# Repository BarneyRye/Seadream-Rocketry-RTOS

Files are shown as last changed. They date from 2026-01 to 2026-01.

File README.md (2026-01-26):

# Seadream Rocketry PCB and Code
 Kicad files include schematic, pcb, extra symbols, footprints 3d files and also the production files for JLCPCB </br>
 Included code written in Platform.io on VSCode, uses prebuilt libaries and freeRTOS, one task for sensor reading and audio, other task for writing to SD

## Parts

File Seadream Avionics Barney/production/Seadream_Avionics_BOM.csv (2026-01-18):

Reference | Qty | Value | DNP | Exclude from BOM | Exclude from Board | Footprint | Datasheet | Description | Part NO.
C1,C3,C4,C5,C6,C7,C12,C13,C14 | 9 | 100nF |  |  |  | Capacitor_SMD:C_0402_1005Metric | https://jlcpcb.com/api/file/downloadByFileSystemAccessId/8579707269996871680 | CL05B104KO5NNNC | C1525
C2,C8,C9,C10 | 4 | 10uF |  |  |  | Capacitor_SMD:C_0603_1608Metric | https://jlcpcb.com/api/file/downloadByFileSystemAccessId/8579707107920437248 | CL10A106KP8NNNC | C19702
C11 | 1 | 22uF |  |  |  | Capacitor_SMD:C_0805_2012Metric | https://jlcpcb.com/api/file/downloadByFileSystemAccessId/8579706866429190144 | CL21A226MAQNNNE | C45783
C15 | 1 | 1uF |  |  |  | Capacitor_SMD:C_0402_1005Metric | https://jlcpcb.com/api/file/downloadByFileSystemAccessId/8579707174974914560 | CL05A105KA5NQNC | C52923
D1,D2,D3 | 3 | LED |  |  |  | LED_SMD:LED_0805_2012Metric | https://jlcpcb.com/api/file/downloadByFileSystemAccessId/8550724080677908480 | NCD0805R1 | C84256
J1,J3 | 2 | B2B-PH-K-S(LF)(SN) |  |  |  | Connector_JST:JST_PH_B2B-PH-K_1x02_P2.00mm_Vertical | https://jlcpcb.com/api/file/downloadByFileSystemAccessId/8588889744620572672 | B2B-PH-K-S(LF)(SN) | C131337
J2 | 1 | TYPE-C16PIN |  |  |  | 2FOOTPRINTS:SHOUHAN_TYPE-C_16PIN_2MD__073_ | https://jlcpcb.com/api/file/downloadByFileSystemAccessId/8588893971980423168 | TYPE-C16PIN | C393939
MICRO_SD1 | 1 | TF-01A |  |  |  | 2FOOTPRINTS:TF-01A | https://jlcpcb.com/api/file/downloadByFileSystemAccessId/8588894212661764096 | TF-01A | C91145
R1,R2,R11 | 3 | 10k |  |  |  | Resistor_SMD:R_0402_1005Metric | https://jlcpcb.com/api/file/downloadByFileSystemAccessId/8588881989415931904 | 0402WGJ0103TCE | C25531
R3,R4 | 2 | 4k7 |  |  |  | Resistor_SMD:R_0402_1005Metric | https://jlcpcb.com/api/file/downloadByFileSystemAccessId/8579705941367193600 | 0402WGF4701TCE | C25900
R5 | 1 | 330 |  |  |  | Resistor_SMD:R_0603_1608Metric | https://jlcpcb.com/api/file/downloadByFileSystemAccessId/8579706223213461504 | 0603WAF3300T5E | C23138
R7,R10 | 2 | 5k1 |  |  |  | Resistor_SMD:R_0402_1005Metric | https://jlcpcb.com/api/file/downloadByFileSystemAccessId/8579706036003409920 | 0402WGF5101TCE | C25905
R8,R9 | 2 | 220 |  |  |  | Resistor_SMD:R_0603_1608Metric | https://jlcpcb.com/api/file/downloadByFileSystemAccessId/8579706178210742272 | 0603WAF2200T5E | C22962
S1 | 1 | KMR221GLFS |  |  |  | 2FOOTPRINTS:SW_KMR221GLFS | https://jlcpcb.com/api/file/downloadByFileSystemAccessId/8588916370310369280 | KMR221GLFS | C72443
SW1 | 1 | SSSS810701 |  |  |  | 2FOOTPRINTS:SW-SMD_SSSS810701 | https://jlcpcb.com/api/file/downloadByFileSystemAccessId/8588917637593751552 | SSSS810701 | C97433
U1 | 1 | BMP280 |  |  |  | 2FOOTPRINTS:XDCR_BMP280 | https://jlcpcb.com/api/file/downloadByFileSystemAccessId/8588881905890156544 | BMP280 | C83291
U2 | 1 | ESP32-S3-MINI-1U-N8 |  |  |  | RF_Module:ESP32-S2-MINI-1U | https://documentation.espressif.com/esp32-s3-mini-1_mini-1u_datasheet_en.pdf | ESP32-S3-MINI-1U-N8 | C2980299
U3 | 1 | LSM6DSO32TR |  |  |  | 2FOOTPRINTS:XDCR_LSM6DSO32TR | https://jlcpcb.com/api/file/downloadByFileSystemAccessId/8588926227138138112 | LSM6DSO32TR | C1864162
U4 | 1 | LD1117S33TR |  |  |  | 2FOOTPRINTS:SOT230P700X180-4N | https://jlcpcb.com/api/file/downloadByFileSystemAccessId/8586198736901459968 | LD1117S33TR | C86781
U5 | 1 | SHT40-AD1B-R3 |  |  |  | 2FOOTPRINTS:SHT4X | https://jlcpcb.com/api/file/downloadByFileSystemAccessId/8588907595537399808 | SHT40-AD1B-R3 | C2848306
U6 | 1 | LD39200PU33R |  |  |  | 2FOOTPRINTS:SON95P300X300X100-7N | https://jlcpcb.com/api/file/downloadByFileSystemAccessId/8588886586771845120 | LD39200PU33R | C222192
U7 | 1 | MAX98357AETE_T |  |  |  | 2FOOTPRINTS:QFN50P300X300X80-17N | https://jlcpcb.com/api/file/downloadByFileSystemAccessId/8588886693302161408 | MAX98357AETE_T | C910544

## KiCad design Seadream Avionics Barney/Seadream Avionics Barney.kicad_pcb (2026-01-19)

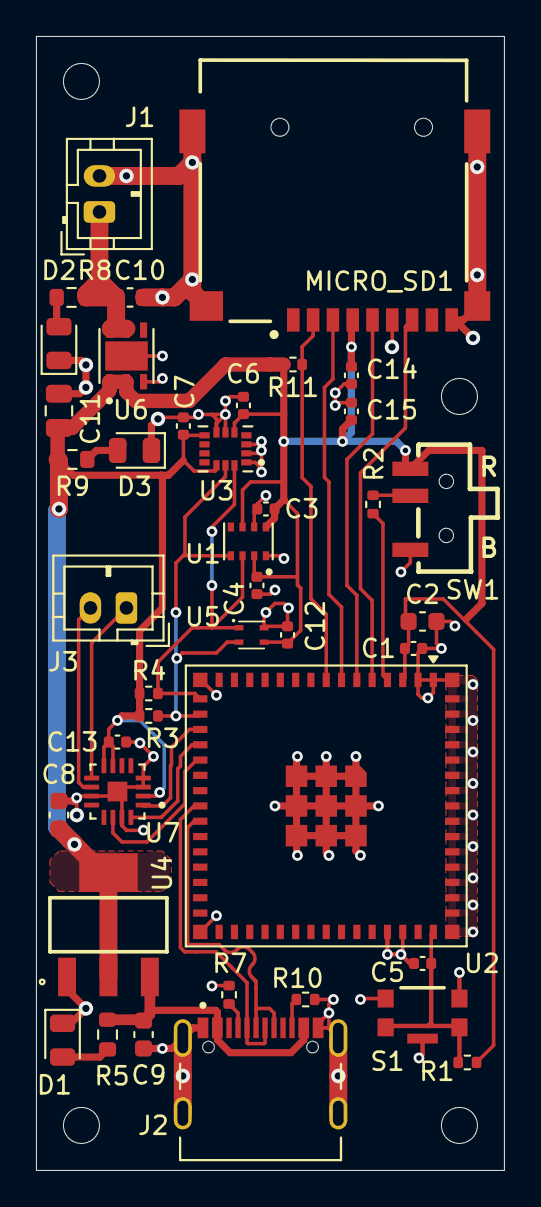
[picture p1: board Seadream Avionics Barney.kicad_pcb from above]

Board: 2 copper layers, 26.0 x 63.0 mm, 41 parts (0 on the bottom side), 25 nets.

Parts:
C1, C3, C4, C5, C6, C7, C12, C13, C14: 100nF; C_0402_1005Metric
C2, C8, C9, C10: 10uF; C_0603_1608Metric
C11: 22uF; C_0805_2012Metric
C15: 1uF; C_0402_1005Metric
D1, D2, D3: LED; LED_0805_2012Metric
J1, J3: B2B-PH-K-S(LF)(SN); JST_PH_B2B-PH-K_1x02_P2.00mm_Vertical
J2: C393939; SHOUHAN_TYPE-C_16PIN_2MD__073_
MICRO_SD1: C91145; TF-01A
R1, R2, R11: 10k; R_0402_1005Metric
R3, R4: 4k7; R_0402_1005Metric
R5: 330; R_0603_1608Metric
R7, R10: 5k1; R_0402_1005Metric
R8, R9: 220; R_0603_1608Metric
S1: KMR221GLFS; SW_KMR221GLFS
SW1: SSSS810701; SW-SMD_SSSS810701
U1: BMP280; XDCR_BMP280
U2: ESP32-S3-MINI-1U-N8; ESP32-S2-MINI-1U
U3: LSM6DSO32TR; XDCR_LSM6DSO32TR
U4: LD1117S33TR; SOT230P700X180-4N
U5: SHT40-AD1B-R3; SHT4X
U6: LD39200PU33R; SON95P300X300X100-7N
U7: MAX98357AETE_T; QFN50P300X300X80-17N

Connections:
+3.3V: C1.2, C2.2, C3.1, C4.1, C6.1, C7.1, C8.1, C11.2, C12.1, C13.1, C14.2, C15.2, MICRO_SD1.4 (VDD), R1.2, R3.1, R4.1, R9.1, R11.1, SW1.3 (C), U1.2 (CSB), U1.6 (VDDIO), U1.8 (VDD), U2.3 (3V3), U3.5 (VDDIO), U3.8 (VDD), U3.12 (CS), U4.2 (OUT), U4.4 (OUT), U5.3 (VDD), U6.1 (OUT), U6.2 (SENSE), U7.2 (GAIN_SLOT), U7.7 (VDD), U7.8 (VDD)
/BOOT: R2.2, U2.4 (IO0)
/CD: MICRO_SD1.2 (CD/DAT3), R11.2, U2.8 (IO4)
/D+: J2.A6 (DP1), J2.B6 (DP2), U2.24 (IO20)
/D-: J2.A7 (DN1), J2.B7 (DN2), U2.23 (IO19)
/EN: C5.2, R1.1, S1.1, S1.4, U2.45 (EN)
/IO12: R4.2, U1.3 (SDI), U2.16 (IO12), U3.14 (SDA), U5.1 (SDA)
/IO13: R3.2, U1.4 (SCK), U2.17 (IO13), U3.13 (SCL), U5.2 (SCL)
/IO14: U2.18 (IO14), U7.1 (DIN)
/IO15: U2.19 (IO15), U7.16 (BCLK)
/IO16: U2.20 (IO16), U7.14 (LRCLK)
/MISO: MICRO_SD1.7 (DAT0), U2.5 (IO1)
/MOSI: MICRO_SD1.3 (CMD), U2.7 (IO3)
/OUT+: J3.1, U7.9 (OUTP)
/OUT-: J3.2, U7.10 (OUTN)
/SCK: MICRO_SD1.5 (CLK), U2.6 (IO2)
/USB 5V: C9.1, J2.A4_B9 (VBUS_A), J2.B4_A9 (VBUS_B), R5.1, U4.3 (IN)
GND: C1.1, C2.1, C3.2, C4.2, C5.1, C6.2, C7.2, C8.2, C9.2, C10.1, C11.1, C12.2, C13.2, C14.1, C15.1, D1.1 (K), D2.1 (K), D3.1 (K), J1.2, J2.A1_B12 (GND_A), J2.B1_A12 (GND_B), J2.SH1 (SHIELD), J2.SH2 (SHIELD), J2.SH3 (SHIELD), J2.SH4 (SHIELD), MICRO_SD1.6 (VSS), MICRO_SD1.CD1 (CD), MICRO_SD1.MP1 (SHIELD), MICRO_SD1.MP2 (SHIELD), MICRO_SD1.MP3 (SHIELD), MICRO_SD1.MP4 (SHIELD), R7.1, R10.2, S1.2, S1.3, S1.5, SW1.1 (A), U1.1 (GND), U1.7 (GND), U2.1 (GND1), U2.2 (GND1), U2.42 (GND1), U2.43 (GND1), U2.46 (GND1), U2.47 (GND1), U2.48 (GND1), U2.49 (GND1), U2.50 (GND1), U2.51 (GND1), U2.52 (GND1), U2.53 (GND1), U2.54 (GND2), U2.55 (GND2), U2.56 (GND2), U2.57 (GND2), U2.58 (GND2), U2.59 (GND2), U2.60 (GND3), U2.61, U2.62 (GND2), U2.63 (GND2), U2.64 (GND2), U2.65 (GND2), U3.1 (SDO/SA0), U3.2 (SDX), U3.3 (SCX), U3.6 (GND), U3.7 (GND), U4.1 (GND), U5.4 (VSS), U6.3 (GND), U6.7 (EXP), U7.3 (GND), U7.4 (SD_MODE), U7.11 (GND), U7.15 (GND), U7.17 (EP)
unnamed: D1.2 (A), R5.2
unnamed: D2.2 (A), R8.2
unnamed: D3.2 (A), R9.2
unnamed: C10.2, J1.1, R8.1, U6.5 (EN), U6.6 (IN)
unnamed: J2.A5 (CC1), R7.2
unnamed: J2.B5 (CC2), R10.1
unnamed: R2.1, SW1.2 (B)

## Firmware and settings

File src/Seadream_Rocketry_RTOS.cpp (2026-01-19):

//If working in arduino IDE, to allow use of esp32 boards
//https://espressif.github.io/arduino-esp32/package_esp32_index.json
//File->Preferences->Additional Board Manager URLs
//Boards Manager -> esp32 by espressif Systems
//Board->ESP32S3 DEV module


//Libaries used and need installing:
/*
Adafruit_LSM6DS
Adafruit SHT4x and dependencies
ESP32 AudioI2S
Adafruit BMP280
*/


//Includes for added libaries
#include <Arduino.h> //Base arduino libary if not using arduino IDE
#include <Wire.h> //I2C protocols
#include <Adafruit_Sensor.h> //Base sensor libary for Adafruit libaries
#include <Adafruit_SHT4x.h> //Temperature and Humidity sensor libaries
#include <Adafruit_LSM6DSO32.h>//Accelerometer and Gyro libary
#include <Adafruit_BMP280.h>//Barometer libary
#include <SD.h> //SD card libary
#include <SPI.h> //SPI libary
#include <Audio.h> //Audio libary
#include <FreeRTOS.h> //FreeRTOS base libary to allow for multitasking
#include <queue.h> //FreeRTOS queue libary for inter-task communication

//Config pins
#define I2C_SDA 12 //I2C pins
#define I2C_SCL 13
#define Audio_DIN 14  //Audio AMP pins
#define Audio_BCLK 15
#define Audio_LRC 16
#define SPI_SCK 2 //SPI/SD card pins
#define SPI_MOSI 3
#define SPI_MISO 1
#define SPI_CS 4

//Log Rates
#define initial_log_rate 50    // Hz, initial logging rate
#define final_log_rate 10      // Hz, reduced logging rate for decent/slower speeds
#define reduce_Hz_time 60      // s, time after which to reduce logging rate, e.g. time to apogee
#define MAX_BUFFER_LINES 5     // No. of data logs per buffer
#define MAX_BUFFER_LENGTH 150  // Length of char buffer lines

//Song timer
#define song_start_time 240  //s, time to start song after startup
#define SONG_PATH "/song.mp3" //Name of song file on SD card

//Object creating from libaries
Adafruit_SHT4x sht4 = Adafruit_SHT4x(); //Temperature and Humidity sensor
Adafruit_LSM6DSO32 imu; //Accelerometer and Gyro
Adafruit_BMP280 bmp; //Barometer
Audio audio; //Audio player

//Data Struct
typedef struct { //struct to store sensor data
  uint32_t time; //TIme of log in ms
  float humidity; //Humidity in %
  float temp_sens; //Temp in C from SHT4x
  float temp_bmp; //Temp in C from BMP180
  float pressure; //Pressure in kPa from BMP180
  float altitude; //Altitude in M from BMP180
  float ax; //Acceleration X in m/s^2
  float ay; //Acceleration Y in m/s^2
  float az; //Acceleration Z in m/s^2
  float gx; //Gyro X in deg/s
  float gy; //Gyro Y in deg/s
  float gz; //Gyro Z in deg/s
} data_struct;

//FreeRTOS Queue
QueueHandle_t logQueue;

//SD Log Filename
char logFilename[15];

//Double Buffers for data logging
data_struct buffer1[MAX_BUFFER_LINES]; // Array of structs to hold data buffers
data_struct buffer2[MAX_BUFFER_LINES];
bool useBuffer1 = true;   // Active buffer flag
uint8_t bufferIndex = 0;  // Index for current buffer

//Fuunction Prototypes
void getNextLogFilename(char* name); //Generate next log filename if log1.csv exists, make log2.csv etc
void getData(data_struct *data_buffer); //Read sensors and fill data struct
void getBufferLine(char *line, data_struct data_buffer); //Converts data struct to string line for block writing to SD card
void char_buffer_write(uint8_t count, data_struct data_buffer, char data_char_buffer[][MAX_BUFFER_LENGTH]); //Writes line to array of char buffers
void audio_start(uint32_t start_time, bool *audio_on); //Checks if it's time to start audio playback
void logRate_reduce(uint32_t *log_rate, bool *reduced, uint32_t loop_start, bool takeoff); //Checks if it's time to reduce log rate and reduces it
void takeoff_detection(bool *takeoff, float initial_altitude); //Detects takeoff based on accelerometer data

//FreeRTOS Tasks
void SensorAudioTask(void *pvParameters); //Core 1 to handle sensor reading and audio playback
void LoggingTask(void *pvParameters); //Core 0 to handle logging data to SD card

//Setup
void setup() {
  Serial.begin(115200); //Begin serial communication
  while(!Serial){delay(10);} //Wait for serial to connect
  Serial.println(F("Initialising...")); //Print initialising message

  //I2C
  Wire.begin(I2C_SDA, I2C_SCL); //Connect I2C to specified pins
  Wire.setClock(100000); //Set I2C clock frequency to 100kHz

  //SPI
  SPI.begin(SPI_SCK, SPI_MISO, SPI_MOSI); //Begin SPI for SD card

  //Accelerometer and Gyro
  if (!imu.begin_I2C()) { Serial.println(F("Failed to find Accelerometer")); } //Begins I2C connection to Accel/Gyro, if fails, print failure to serial
  imu.setAccelDataRate(LSM6DS_RATE_52_HZ); //Sets accelerometer data rate to 52Hz
  imu.setAccelRange(LSM6DSO32_ACCEL_RANGE_32_G); //Sets accelerometer range to 32G
  imu.setGyroDataRate(LSM6DS_RATE_52_HZ); //Sets gyro data rate to 52Hz
  imu.setGyroRange(LSM6DS_GYRO_RANGE_2000_DPS); //Sets gyro range to 2000 degrees per second

  //Barometer
  if (!bmp.begin(0x76)) { Serial.println(F("Failed to find Barometer")); } //Begins I2C connection to Barometer, if fails, print failure to serial
  else{
    bmp.setSampling(Adafruit_BMP280::MODE_NORMAL,
                    Adafruit_BMP280::SAMPLING_X1,
                    Adafruit_BMP280::SAMPLING_X1,    
                    Adafruit_BMP280::FILTER_OFF,  
                    Adafruit_BMP280::STANDBY_MS_1); 
  }
  //Temperature and Humidity Sensor
  if (!sht4.begin(&Wire)) { Serial.println(F("Temperature/Humidity sensor not found")); } //Begins I2C connection to Temp/Humidity sensor, if fails, print failure to serial

  //SD CARD
  if (!SD.begin(SPI_CS)) { //Begins SD card connection, if fails, print failure to serial
    Serial.println(F("SD Card not found"));
  } 
  else {
    getNextLogFilename(logFilename); //Get next available log filename
    Serial.print(F("Log file: ")); Serial.println(logFilename); //Prints log filename to serial
    File f = SD.open(logFilename, FILE_WRITE); //Opens/creates file for writing
    if (f) { //If file opened successfully
      //Write CSV header line
      f.println("Time_ms,Humidity_%,Temp_C,Temp_BMP_C,Pressure_kPa,Altitude_M,Accel_X,Accel_Y,Accel_Z,Gyro_X,Gyro_Y,Gyro_Z");
      f.close(); //Closes file
    } else {
      Serial.println(F("Failed to open log file")); //Prints failure message to serial
    }
  }

  //Audio
  audio.setPinout(Audio_BCLK, Audio_LRC, Audio_DIN); //Connects audio AMP to specified pins
  audio.setVolume(10);  // 1-21, Sets volume

  //FreeRTOS Queue
  logQueue = xQueueCreate(2, sizeof(bool)); //Create queue to hold 2 buffer ready flags

  //Create FreeRTOS Tasks
  xTaskCreatePinnedToCore(SensorAudioTask, "SensorAudioTask", 4096, NULL, 1, NULL, 1);  // Core 1 for sensors and audio
  xTaskCreatePinnedToCore(LoggingTask, "LoggingTask", 4096, NULL, 1, NULL, 0);          // Core 0 for logging

  Serial.println(F("Finished Initialising")); //Print finished initialising message
}

//Loop
void loop() {
  //Nothing here, all handled by FreeRTOS tasks
}
//Sensor and Audio Task
void SensorAudioTask(void *pvParameters) {
  static bool audio_on = false; //Audio playback flag
  static bool takeoff = false; //Takeoff detected flag
  static uint32_t log_rate = 1000 / initial_log_rate; //Sets initial log rate in ms, converts from Hz
  static bool reduced = false; //Log rate reduced flag
  static uint32_t last_log = 0; //Last log time
  static float initial_altitude = 0.0f; //Initial altitude at startup, used for takeoff detection, value gotten after first data colelction
  static bool first_run = false; //Flag to indicate first run of data collection got intial altitude
  static uint32_t loop_start = millis(); //Loop start time

  for (;;) { //Infinite loop for task
    //Audio Playback
    if (!audio_on) {audio_start(loop_start, &audio_on);} //If audio isn't on, check if it's time to start and start if so
    if (audio_on) { //If audio is on, call audio loop to keep playing
      audio.loop();
      if (!audio.isRunning()) { //If audio has finished playing
        audio.connecttoFS(SD, SONG_PATH); //Restart song
      }
    }

    //Log Rate Reduction
    if (!reduced) logRate_reduce(&log_rate, &reduced, loop_start, takeoff); //If log rate hasn't been reduced yet, check if it's time to reduce it and reduce if so
     
    //Data Logging
    if (millis() - last_log >= log_rate) { //If it's time to log data, i.e. time since last log >= log rate
      uint32_t now = millis(); //Time for current logging iteration
      static uint32_t data_start = now; //First data log time
      
      //Read Sensors and fill data struct
      data_struct data; //Create data struct for current iteration
      data.time = now - data_start; //Stores time since start in data struct
      getData(&data); //Fills data struct with sensor data using function

      last_log = now; //Sets last log time to now

      //Print data to serial for debugging
      Serial.print("Time: "); Serial.print(data.time);
      Serial.print(" ms, Humidity: "); Serial.print(data.humidity); Serial.print(" %, Temp: "); Serial.print(data.temp_sens); Serial.print(" C");
      Serial.print(", Temp_BMP: "); Serial.print(data.temp_bmp); Serial.print(" C, Pressure: "); Serial.print(data.pressure); Serial.print(" kPa, Altitude: "); Serial.print(data.altitude); Serial.print(" m");
      Serial.print(", Accel (m/s^2): X "); Serial.print(data.ax); Serial.print(" Y "); Serial.print(data.ay); Serial.print(" Z "); Serial.print(data.az);
      Serial.print(", Gyro (deg/s): X "); Serial.print(data.gx); Serial.print(" Y "); Serial.print(data.gy); Serial.print(" Z "); Serial.println(data.gz); 

      //Fill active buffer
      if (useBuffer1) { //If flag is true, fill buffer1
        buffer1[bufferIndex] = data; //Copy data struct to buffer1 at current index
      } else { //Else fill buffer2
        buffer2[bufferIndex] = data; //Copy data struct to buffer2 at current index
      }
      bufferIndex++; //Increases buffer index

      //If buffer full, send to logging task
      if (bufferIndex >= MAX_BUFFER_LINES) {
        bool readyBuffer = useBuffer1;  // Sets flag for which buffer is ready
        xQueueSend(logQueue, &readyBuffer, portMAX_DELAY); //Sends ready buffer flag to logging task
        bufferIndex = 0; //Resets buffer index
        useBuffer1 = !useBuffer1;  //Swap active buffer to fill
      }
      initial_altitude = data.altitude; //Initial altitude at startup
      first_run = true;
    }

    if (!takeoff && first_run) { //Calls takeoff detection function to update takeoff flag
      takeoff_detection(&takeoff, initial_altitude);
      loop_start = millis(); //Reset loop start time untill takeoff detected
    }
    vTaskDelay(1);  //Yield to other tasks
  }
}

//Logging Task
void LoggingTask(void *pvParameters) {
  char data_char_buffer[MAX_BUFFER_LINES][MAX_BUFFER_LENGTH]; //Char buffer array for block writing to SD card

  for (;;) { //Infinite loop for task
    bool readyBuffer; //Variable to hold which buffer is ready
    if (xQueueReceive(logQueue, &readyBuffer, portMAX_DELAY) == pdPASS) { //Waits for ready buffer flag from sensor task
      data_struct *buffer = readyBuffer ? buffer1 : buffer2; //if readyBuffer is true, use buffer1, else use buffer2

      //Convert data structs to char buffer lines
      for (uint8_t i = 0; i < MAX_BUFFER_LINES; i++) { //Loops between buffer lines
        char_buffer_write(i, buffer[i], data_char_buffer); //Converts struct data lines to char buffer lines and inserts into corressponding index
      }

      //Write char buffer lines to SD card
      File f = SD.open(logFilename, FILE_APPEND); //Opens log file for appending
      if (f) { //If file opened successfully
        for (uint8_t i = 0; i < MAX_BUFFER_LINES; i++) { //Loops between buffer lines
          f.println(data_char_buffer[i]); //Writes char buffer line to file
        }
        f.close(); //Closes file
      }
    }
  }
}

//Helper Functions
void getNextLogFilename(char *name) { //Gets next available log filename
  uint8_t index = 1; //Starts at log1.csv
  char temp_name[15]; //Temporary filename storage
  while (true) { //Infinite loop until available filename found, doesn't slow logging as done before looping starts
    sprintf(temp_name,"/log%d.csv",index); //Creates filename string from index
    if (!SD.exists(temp_name)){ //If file doesn't exist, copy to output and return
      strcpy(name, temp_name); //Copy temporary name to output
      return; //Exit function
    }
    index++; //Increase index and try again
  }
}

void audio_start(uint32_t start_time, bool *audio_on) { //Checks if it's time to start audio playback
  if (millis() - start_time >= (song_start_time * 1000)) { //If time since start >= song start time
    audio.connecttoFS(SD, SONG_PATH); //Connect to song file on SD card and start playing
    *audio_on = true; //Set audio on flag to true
  }
}

void takeoff_detection(bool *takeoff, float initial_altitude) { //Detects takeoff based on accelerometer data
  if (useBuffer1){
    if (buffer1[bufferIndex].altitude - initial_altitude > 10){ //If altitude has increased by more than 10m since start
      *takeoff = true; //Sets takeoff flag to true
    }
  }
  else{
    if (buffer2[bufferIndex].altitude - initial_altitude > 10){ //If altitude has increased by more than 10m since start
      *takeoff = true; //Sets takeoff flag to true
    }
  }
}

void logRate_reduce(uint32_t *log_rate, bool *reduced, uint32_t loop_start, bool takeoff) { //Checks if it's time to reduce log rate and reduces it
  if ((millis() - loop_start >= (reduce_Hz_time * 1000)) && takeoff) { //If time since start >= reduce time
    *log_rate = 1000 / final_log_rate; //Sets log rate to final log rate in ms, converts from Hz
    *reduced = true; //Sets reduced flag to true
    bmp.setSampling(Adafruit_BMP280::MODE_NORMAL,     
                    Adafruit_BMP280::SAMPLING_X2,   
                    Adafruit_BMP280::SAMPLING_X16, 
                    Adafruit_BMP280::FILTER_X16,     
                    Adafruit_BMP280::STANDBY_MS_63);
  }
  imu.setAccelDataRate(LSM6DS_RATE_12_5_HZ); //Sets accelerometer data rate to 12.5Hz
  imu.setGyroDataRate(LSM6DS_RATE_12_5_HZ); //Sets gyro data rate to 12.5Hz
}

void getData(data_struct *data_buffer) { //Reads sensors and fills data struct
  //Accelerometer and Gyro
  sensors_event_t accel, gyro, temp_imu; //Create sensor event structs
  imu.getEvent(&accel, &gyro, &temp_imu); //Reads sensor data into structs
  data_buffer->ax = accel.acceleration.x; //Fills data struct with accel and gyro data
  data_buffer->ay = accel.acceleration.y;
  data_buffer->az = accel.acceleration.z;
  data_buffer->gx = gyro.gyro.x;
  data_buffer->gy = gyro.gyro.y;
  data_buffer->gz = gyro.gyro.z;

  //Barometer
  data_buffer->temp_bmp = bmp.readTemperature(); //Reads data from BMP280 and fills data struct
  data_buffer->pressure = bmp.readPressure() / 1000; //Convert Pa to kPa
  data_buffer->altitude = bmp.readAltitude(1013.25); //Assumes sea level pressure of 101325 Pa

  //Temperature and Humidity Sensor
  sensors_event_t humidity, temp; //Create sensor event structs
  sht4.getEvent(&humidity, &temp); //Reads sensor data into structs
  data_buffer->humidity = humidity.relative_humidity; //Fills data struct with temp and humidity data
  data_buffer->temp_sens = temp.temperature;
}

void getBufferLine(char *line, data_struct data_buffer) { //Converts data struct to string line for block writing to SD card
  snprintf(line, MAX_BUFFER_LENGTH, //line is where the string is stored, MAX_BUFFER_LENGTH is max length of line
    "%lu,%.2f,%.2f,%.2f,%.2f,%.2f,%.3f,%.3f,%.3f,%.3f,%.3f,%.3f", //Format string for CSV line, with 2 decimal places for floats except 3 for accel/gyro
    data_buffer.time, //Corressponding data struct values to store in line
    data_buffer.humidity,
    data_buffer.temp_sens,
    data_buffer.temp_bmp,
    data_buffer.pressure,
    data_buffer.altitude,
    data_buffer.ax,
    data_buffer.ay,
    data_buffer.az,
    data_buffer.gx,
    data_buffer.gy,
    data_buffer.gz);
}

void char_buffer_write(uint8_t count, data_struct data_buffer, char data_char_buffer[][MAX_BUFFER_LENGTH]) { //Writes line to array of char buffers
  char line[MAX_BUFFER_LENGTH]; //Temporary line buffer
  getBufferLine(line, data_buffer); //Gets data line from data struct
  strcpy(data_char_buffer[count], line); //Copies line to char buffer array at specified index
}

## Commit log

2026-01-12 Edited so Serial prints over USB rather than UART
2026-01-12 Changed BMP180 for BMP280, and added calibration settings to BMP and IMU
2026-01-14 Changed I2C Speed
2026-01-18 Added more info to BOM for JLCPCB PCBA
    [Seadream Avionics Barney.kicad_pcb, Seadream Avionics Barney.kicad_sch, bom.csv]
2026-01-18 Changed file names
    [Seadream_Avionics_BOM.csv, Seadream_Avionics_P&P.csv, positions.csv]
2026-01-19 Added logo
    [Seadream Avionics Barney.kicad_pcb, designators.csv, positions.csv]
2026-01-27 Added connection flags to sensors
2026-02-05 Added landing detection
